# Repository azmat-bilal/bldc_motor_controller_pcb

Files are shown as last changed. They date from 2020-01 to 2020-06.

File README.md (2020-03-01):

# bldc_motor_controller_pcb
A Brushless DC Motor controller board. The design is inspired and is compatible with Odrive project (https://github.com/madcowswe/ODriveHardware) except that this one is single channel.

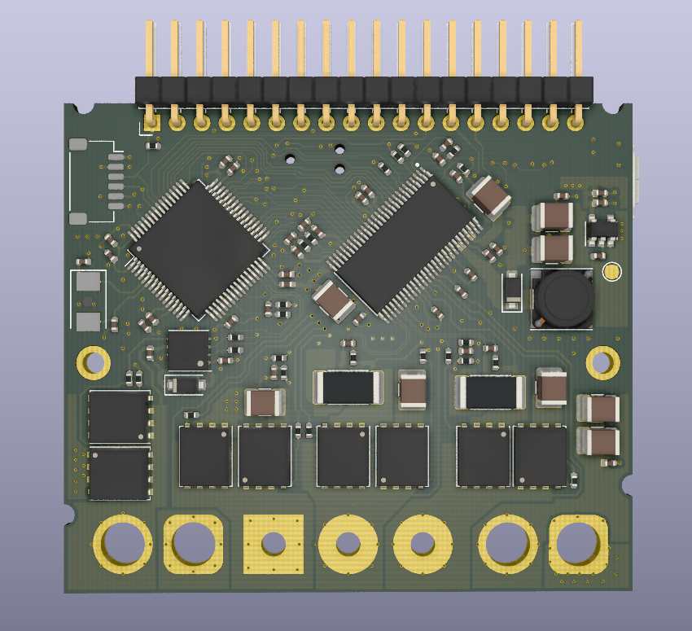
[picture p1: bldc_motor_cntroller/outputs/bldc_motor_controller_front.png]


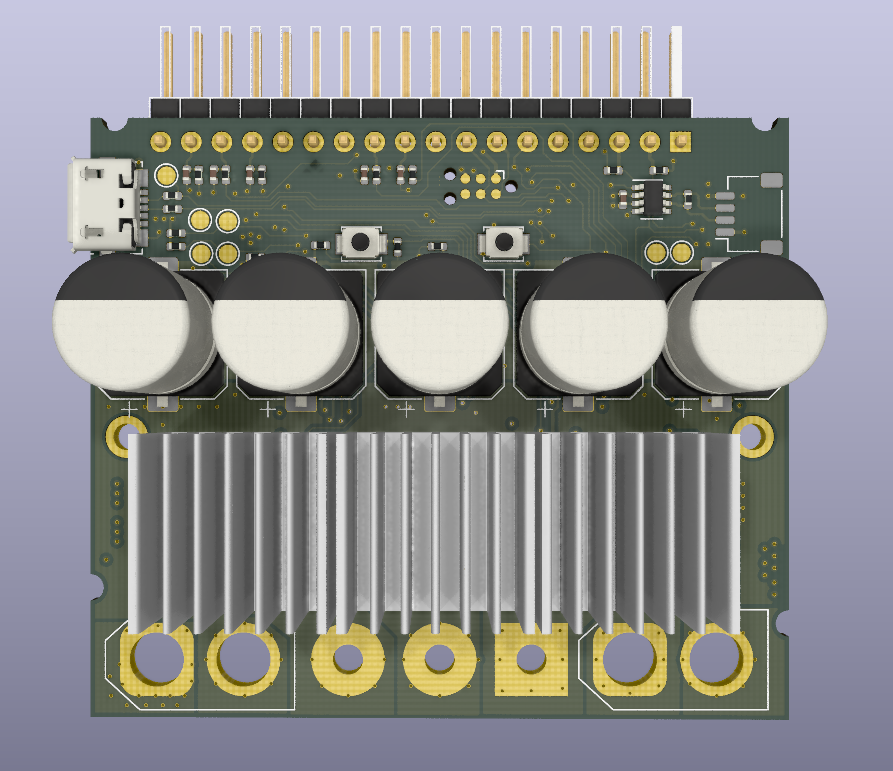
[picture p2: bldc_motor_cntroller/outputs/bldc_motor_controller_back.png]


# Sponsorship
Huge thanks to Mouser Elecotronics (www.mouser.com) to sponsor components to build and test the design.

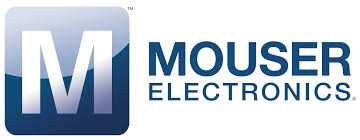
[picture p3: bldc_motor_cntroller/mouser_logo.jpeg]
Sponsor


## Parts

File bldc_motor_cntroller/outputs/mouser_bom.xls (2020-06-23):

BASKET:02.03.2020 00:00:16
Mouser No | Mfr. No | Manufacturer | Customer No | Description | RoHS | Lifecycle | Order Qty. | Price (EUR) | Ext.: (EUR)
80-C0402C223K5R7411 | C0402C223K5RAC7411 | KEMET |  | Multilayer Ceramic Capacitors MLCC - SMD/SMT 50V 0.022uF X7R 0402 10% | RoHS Compliant |  | 2 | 0,234 € | 0,47 €
80-C0402C222J3GECLR | C0402C222J3GEC7411 | KEMET | C37, C41, C45, C46 | Multilayer Ceramic Capacitors MLCC - SMD/SMT 25V 2200pF C0G 0402 5% AEC-Q200 | RoHS Compliant |  | 8 | 0,171 € | 1,37 €
80-C1210C225K1RAUTO | C1210C225K1RACAUTO | KEMET | C42, C43, C44 | Multilayer Ceramic Capacitors MLCC - SMD/SMT 100V 2.2uF X7R 1210 10% AEC-Q200 | RoHS Compliant |  | 6 | 0,603 € | 3,62 €
667-EEH-ZS1J151P | EEH-ZS1J151P | Panasonic | C7, C8, C9, C10, C58 | Aluminium Organic Polymer Capacitors 63VDC 150uF 125degC Hybrid Cap AEC-Q200 | RoHS Compliant | New Product | 10 | 1,47 € | 14,70 €
81-GCM155L8EH104KE7D | GCM155L8EH104KE07D | Murata | C28, C29, C31, C32 | Multilayer Ceramic Capacitors MLCC - SMD/SMT | RoHS Compliant |  | 8 | 0,09 € | 0,72 €
81-GCM155R71E153JA5D | GCM155R71E153JA55D | Murata | C40 | Multilayer Ceramic Capacitors MLCC - SMD/SMT 0402 0.015uF 25volts X7R 5% | RoHS Compliant |  | 2 | 0,09 € | 0,18 €
81-GCQ1555C1H120FB1D | GCQ1555C1H120FB01D | Murata | C56, C57 | Multilayer Ceramic Capacitors MLCC - SMD/SMT 0402 50VDC 12pF 1% AEC-Q200 | RoHS Compliant |  | 4 | 0,486 € | 1,94 €
963-GMK105CC6105MV-F | GMK105CC6105MV-F | Taiyo Yuden | C2 | Multilayer Ceramic Capacitors MLCC - SMD/SMT 0402 35VDC 1uF 20% X6S | RoHS Compliant | New Product | 14 | 0,094 € | 1,32 €
81-GRM1555C1H271FA1D | GRM1555C1H271FA01D | Murata | C14, C39 | Multilayer Ceramic Capacitors MLCC - SMD/SMT 270pF 50Volts C0G 1% | RoHS Compliant |  | 4 | 0,189 € | 0,76 €
81-GRM155C81E225KE1D | GRM155C81E225KE11D | Murata | C15, C21 | Multilayer Ceramic Capacitors MLCC - SMD/SMT 0402 2.2uF 25volts *Derate Voltage/Temp | RoHS Compliant |  | 12 | 0,165 € | 1,98 €
81-GRM155R62A104KE4D | GRM155R62A104KE14D | Murata | C1 | Multilayer Ceramic Capacitors MLCC - SMD/SMT 0402 0.10uF 100volts *Derate Voltage/Temp | RoHS Compliant |  | 26 | 0,032 € | 0,83 €
81-GRM32EC81C476KE5L | GRM32EC81C476KE15L | Murata | C34, C35 | Multilayer Ceramic Capacitors MLCC - SMD/SMT 1210 47uF 16volts *Derate Voltage/Temp | RoHS Compliant |  | 4 | 0,702 € | 2,81 €
963-HMK325C7475KN-TE | HMK325C7475KN-TE | Taiyo Yuden | C25, C27 | Multilayer Ceramic Capacitors MLCC - SMD/SMT 1210 100VDC 4.7uF 10% X7S | RoHS Compliant |  | 4 | 1,13 € | 4,52 €
77-VJ0402A820JXACBC | VJ0402A820JXACW1BC | Vishay | C1, C2, C3, C4, C5, C | Multilayer Ceramic Capacitors MLCC - SMD/SMT 0402 82pF 50volts C0G 5% | RoHS Compliant |  | 12 | 0,09 € | 1,08 €
71-CRCW04020000Z0EDC | CRCW04020000Z0EDC | Vishay | R1, R2, R6, R7, R8 | Thick Film Resistors - SMD 1/16watt 0ohm Commercial Use | RoHS Compliant By Exemption |  | 10 | 0,014 € | 0,14 €
71-CRCW040210K0FKEDC | CRCW040210K0FKEDC | Vishay | R11, R13, R25, R26, R | Thick Film Resistors - SMD 1/16watt 10Kohms 1% Commercial Use | RoHS Compliant By Exemption |  | 14 | 0,029 € | 0,41 €
71-CRCW0402-18K-E3 | CRCW040218K0FKED | Vishay | R22, R24 | Thick Film Resistors - SMD 1/16watt 18Kohms 1% | RoHS Compliant By Exemption |  | 4 | 0,09 € | 0,36 €
71-CRCW0402220KFKEDC | CRCW0402220KFKEDC | Vishay | R20 | Thick Film Resistors - SMD 1/16watt 220Kohms 1% Commercial Use | RoHS Compliant By Exemption |  | 2 | 0,09 € | 0,18 €
71-CRCW040222R0FKEDC | CRCW040222R0FKEDC | Vishay | R9, R10 | Thick Film Resistors - SMD 1/16watt 22ohms 1% Commercial Use | RoHS Compliant By Exemption |  | 8 | 0,09 € | 0,72 €
71-CRCW04022R20FKEDC | CRCW04022R20FKEDC | Vishay | R15, R18, R33, R34, R | Thick Film Resistors - SMD 1/16watt 2.2ohms 1% Commercial Use | RoHS Compliant By Exemption |  | 16 | 0,086 € | 1,38 €
71-CRCW04023K30FKEDC | CRCW04023K30FKEDC | Vishay | R3, R4, R5, R16, R17, | Thick Film Resistors - SMD 1/16watt 3.3Kohms 1% Commercial Use | RoHS Compliant By Exemption |  | 18 | 0,029 € | 0,52 €
279-CRGP0402F47K | CRGP0402F47K | TE Connectivity | R30 | Thick Film Resistors - SMD CRGP 0402 47K 1% SMD Resistor | RoHS Compliant |  | 2 | 0,09 € | 0,18 €
652-CSS2H2512RL500F | CSS2H-2512R-L500F | Bourns | R41, R42 | Current Sense Resistors - SMD 0.5mOHMS 6W 1% AEC-Q200 | RoHS Compliant |  | 4 | 0,837 € | 3,35 €
667-ERJ-2RKF1001X | ERJ-2RKF1001X | Panasonic | R14, R21 | Thick Film Resistors - SMD 0402 1Kohms 1% AEC-Q200 | RoHS Compliant By Exemption |  | 4 | 0,09 € | 0,36 €
667-ERJ-2RKF1200X | ERJ-2RKF1200X | Panasonic | R12, R39, R40 | Thick Film Resistors - SMD 0402 120ohms 1% AEC-Q200 | RoHS Compliant By Exemption |  | 6 | 0,09 € | 0,54 €
963-NR6045T330M | NR6045T330M | Taiyo Yuden | L1 | Fixed Inductors 6045 33uH 188.5mOhms +/-20%Tol 1.4A HiCur | RoHS Compliant |  | 2 | 0,387 € | 0,77 €
863-MBR140SFT1G | MBR140SFT1G | ON Semiconductor | D1 | Schottky Diodes & Rectifiers 1A 40V | RoHS Compliant |  | 2 | 0,36 € | 0,72 €
863-MBR2H100SFT3G | MBR2H100SFT3G | ON Semiconductor | D2 | Schottky Diodes & Rectifiers 2A 100V | RoHS Compliant |  | 2 | 0,396 € | 0,79 €
595-DRV8301DCAR | DRV8301DCAR | Texas Instruments | U4 | Motor/Motion/Ignition Controllers & Drivers 3-PHASE BRUSHLESS MOTOR PRE-DRIVER | RoHS Compliant |  | 2 | 5,26 € | 10,52 €
926-LM5109BSDX/NOPB | LM5109BSDX/NOPB | Texas Instruments | U3 | Gate Drivers | RoHS Compliant |  | 2 | 1,18 € | 2,36 €
511-STM32F405RGT7 | STM32F405RGT7 | STMicroelectronics | U5 | ARM Microcontrollers - MCU 16/32-BITS MICROS | RoHS Compliant |  | 2 | 9,86 € | 19,72 €
595-TCAN332GDCNT | TCAN332GDCNT | Texas Instruments | U1 | CAN Interface IC | RoHS Compliant |  | 2 | 2,44 € | 4,88 €
595-TLV75733PDBVR | TLV75733PDBVR | Texas Instruments | U2 | LDO Voltage Regulators 1-A low-IQ small-size low-dropout (LDO) regulator 5-SOT-23 -40 to 125 | RoHS Compliant |  | 2 | 0,522 € | 1,04 €
581-CX532GB8HHPQZ1 | CX5032GB08000H0HPQZ1 | Kyocera | Y1 | Crystals 08000kHz 12pF With Thermistor | RoHS Compliant |  | 2 | 0,72 € | 1,44 €
653-B3U-1000P-B | B3U-1000P-B | Omron | SW1, SW2 | Tactile Switches Top Actuated with boss w/o ground | RoHS Compliant |  | 4 | 0,873 € | 3,49 €
595-CSD18540Q5BT | CSD18540Q5BT | Texas Instruments | Q1, Q2, Q3, Q4, Q5, Q | MOSFET 60V,NCh NexFET Pwr MOSFET | RoHS Compliant By Exemption |  | 16 | 2,05 € | 32,80 €
538-47346-0001 | 47346-0001 | Molex | J5 | USB Connectors MICRO USB B RECPT BTTM MOUNT ASSY | RoHS Compliant |  | 2 | 0,855 € | 1,71 €
810-C3225X7R1N106K25 | C3225X7R1N106K250AC | TDK |  | Multilayer Ceramic Capacitors MLCC - SMD/SMT 1210 75VDC 10uF 10% X7R | RoHS Compliant | New Product | 4 | 0,954 € | 3,82 €
985-AS5047P-ATSM | AS5047P-ATSM | ams | U1 | Board Mount Hall Effect/Magnetic Sensors 14 bit core res Up to 28krpm | RoHS Compliant |  | 2 | 10,72 € | 21,44 €

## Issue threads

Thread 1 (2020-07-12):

Rough cost estimate of 10 boards

happytm, 2020-07-12:
can you please provide rough estimate of 10 boards including parts  & PCB's ?

Thanks.

azmat-bilal, 2020-08-24:
i have added mouser BOM (with mouser part numbers). it can be used to estimate realtime cost for 10 units using https://eu.mouser.com/create-bom/

azmat-bilal, 2020-08-24:
for PCBs, it depends on the manufacturer and leadtime. its a simple 4 layer pcb so shouldnt cost more than 200 euros.

happytm, 2020-08-24:
@azmat-bilal  Thanks.

Closed 2020-08-24.

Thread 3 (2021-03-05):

Corresponding to which version and voltage of ODrive?

TDA-2030, 2021-03-05:
Recently, I plan to flash firmware to the board, but I can't find version info on silk screen, so I don't know which firmware to download [here](https://github.com/odriverobotics/ODrive/releases). Please point out the correct firmware.

azmat-bilal, 2021-03-17:
i have tested it with v0.4.1. it should also work with v0.4.11.

for versions v0.5+ it will not work out of the box as there is a firmware change were the controller waits for both drivers to get online at boot. there is a short fix mentioned in detail here https://discourse.odriverobotics.com/t/solved-new-firmware-odrive-tool-v5-1-for-3-4-24v-custom-board-one-axis/5805

Closed 2021-03-17.

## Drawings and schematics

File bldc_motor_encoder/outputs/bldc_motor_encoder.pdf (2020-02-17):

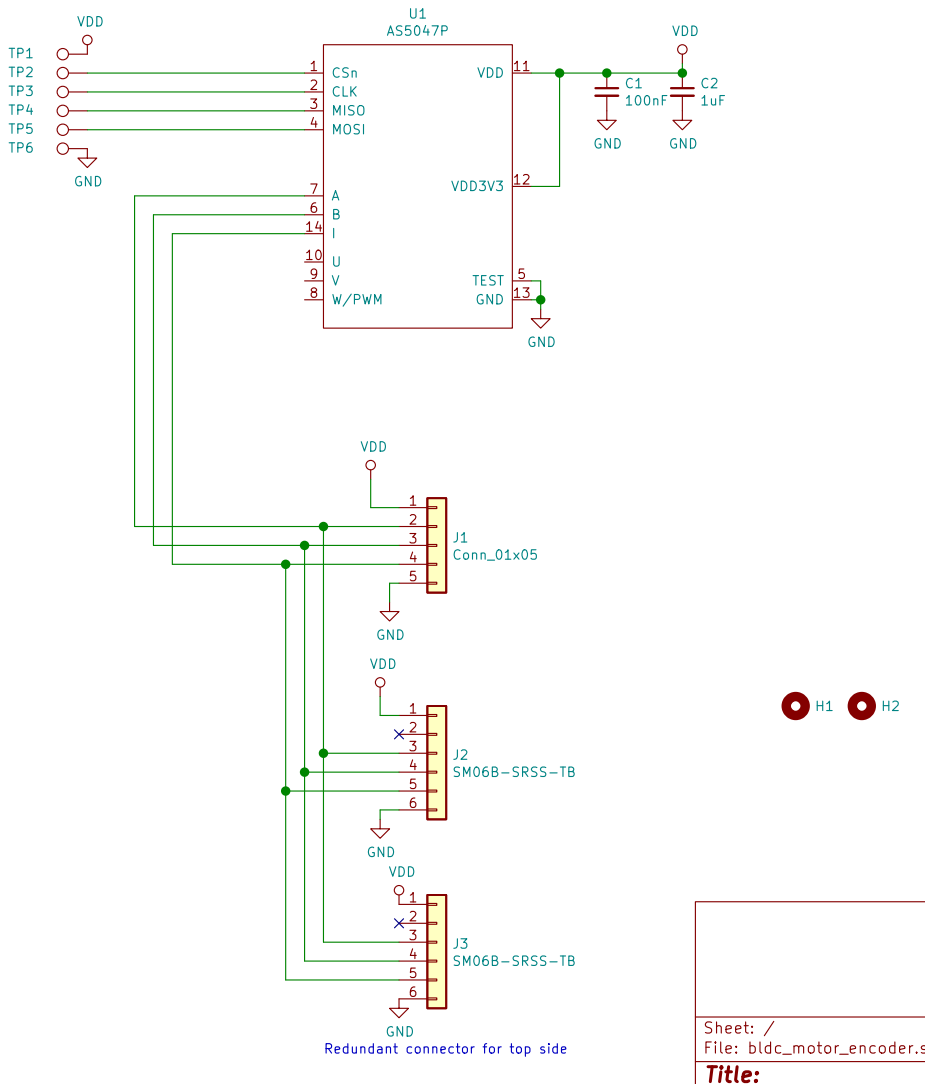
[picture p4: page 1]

1uF Redundant connector for top side

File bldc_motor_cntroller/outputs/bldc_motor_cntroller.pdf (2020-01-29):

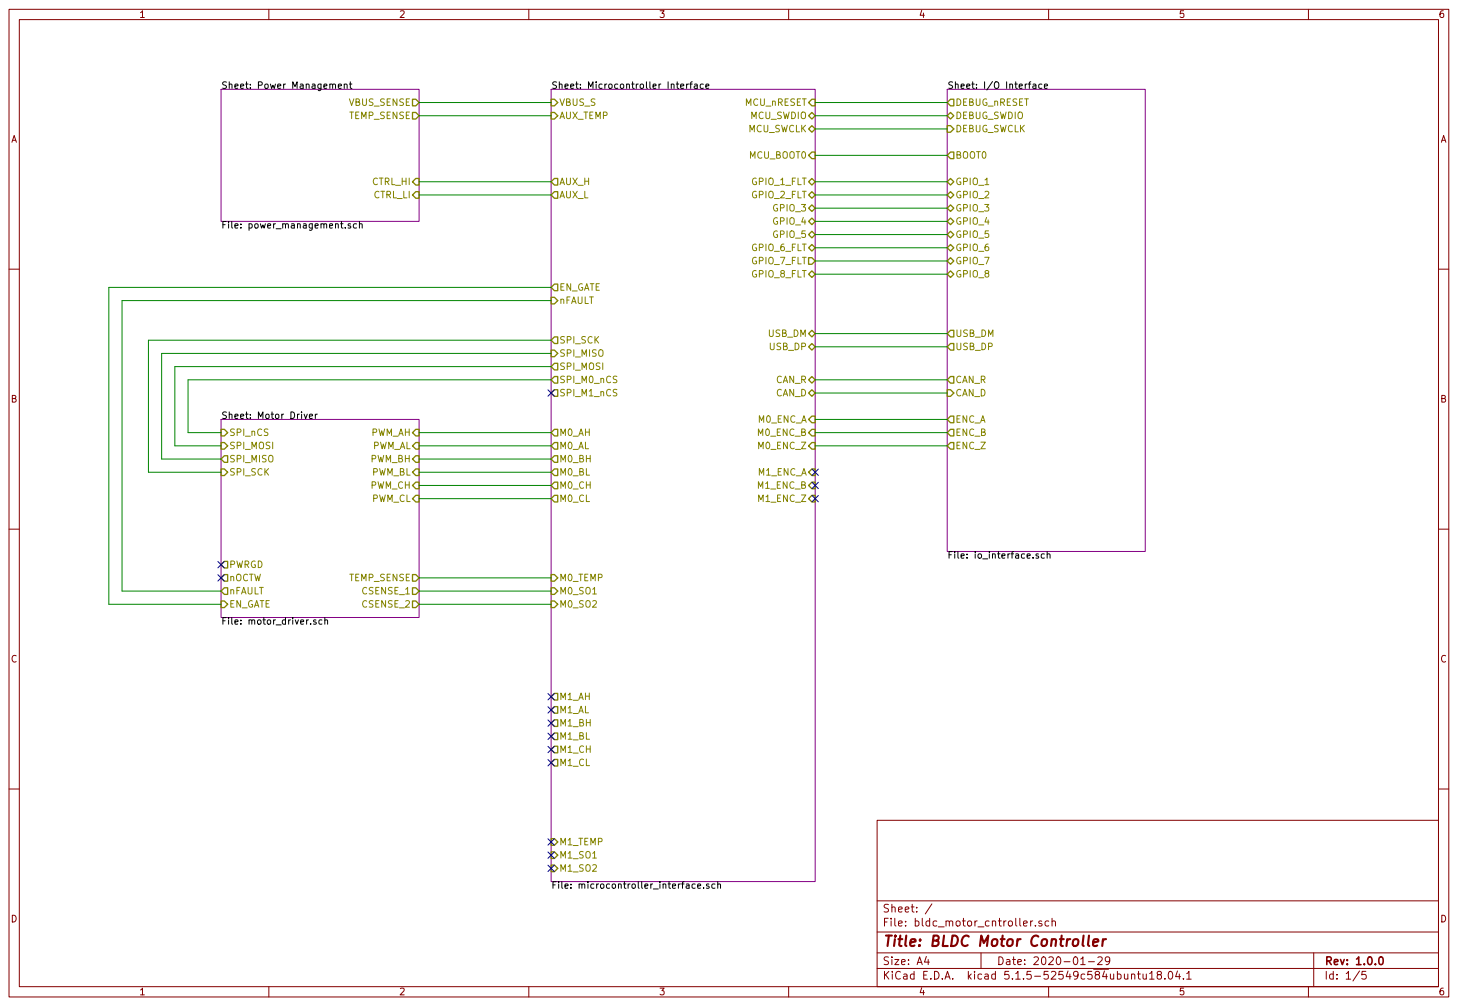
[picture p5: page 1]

Sheet: I/O Interface File: io_interface.sch GPIO_1 GPIO_2 GPIO_7 GPIO_8 GPIO_3 GPIO_6 GPIO_4 GPIO_5 DEBUG_SWDIO
DEBUG_SWCLK DEBUG_nRESET BOOT0 USB_DP USB_DM

File: bldc_motor_cntroller.sch Sheet: /
Id: 1/5 Title: BLDC Motor Controller

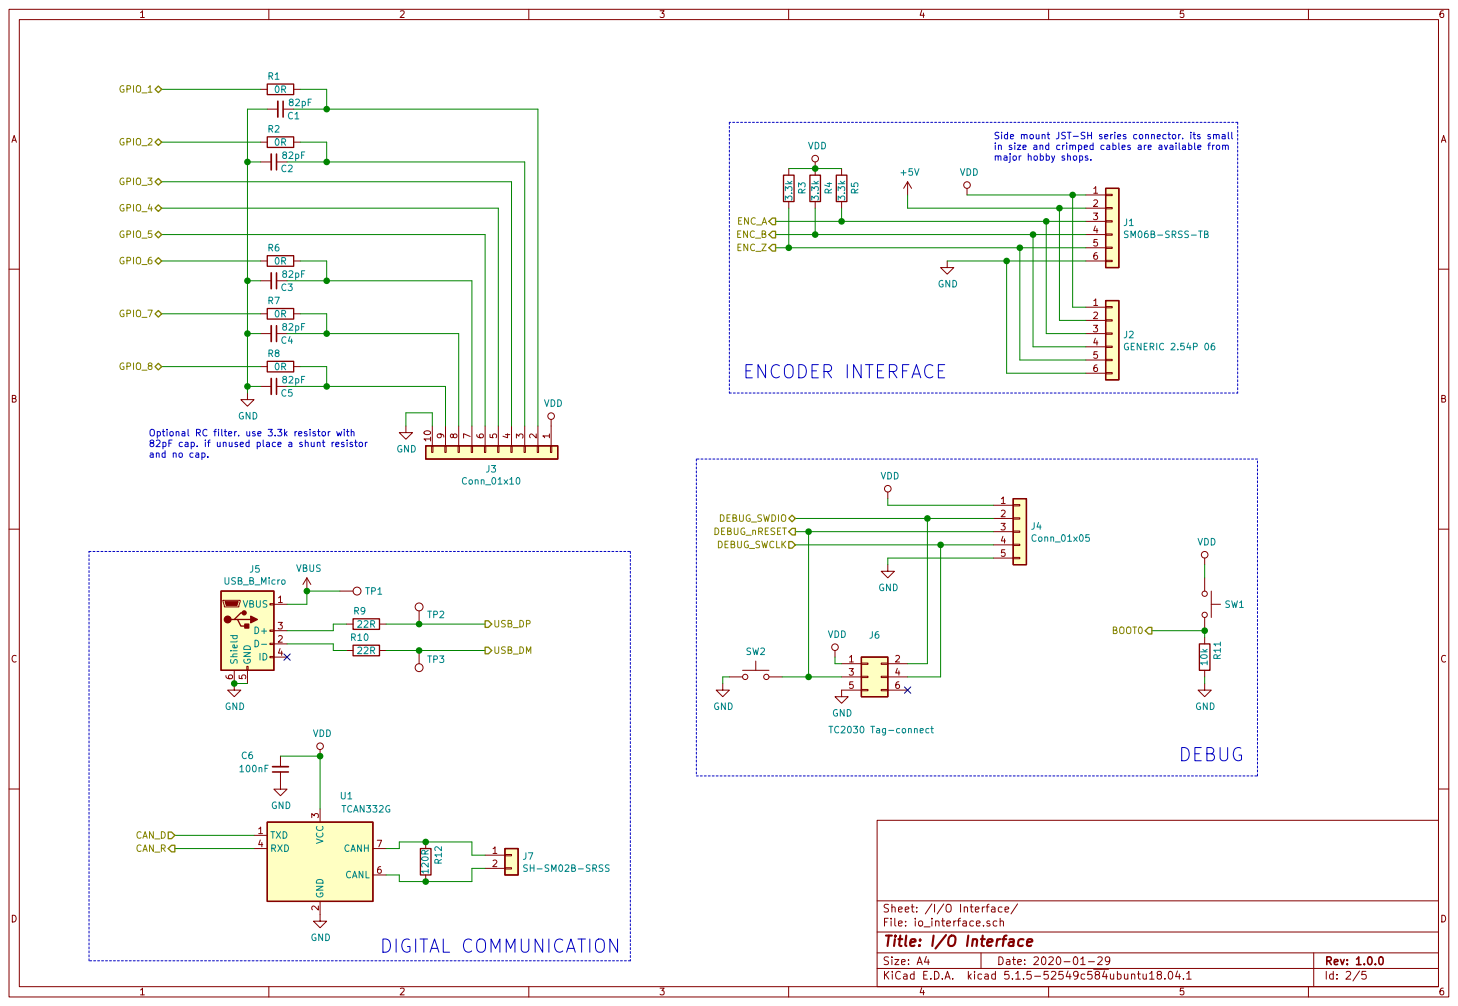
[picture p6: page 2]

Side mount JST-SH series connector. its small
in size and crimped cables are available from
major hobby shops.

Optional RC filter. use 3.3k resistor with
82pF cap. if unused place a shunt resistor
and no cap.

File: io_interface.sch Sheet: /I/O Interface/ GND

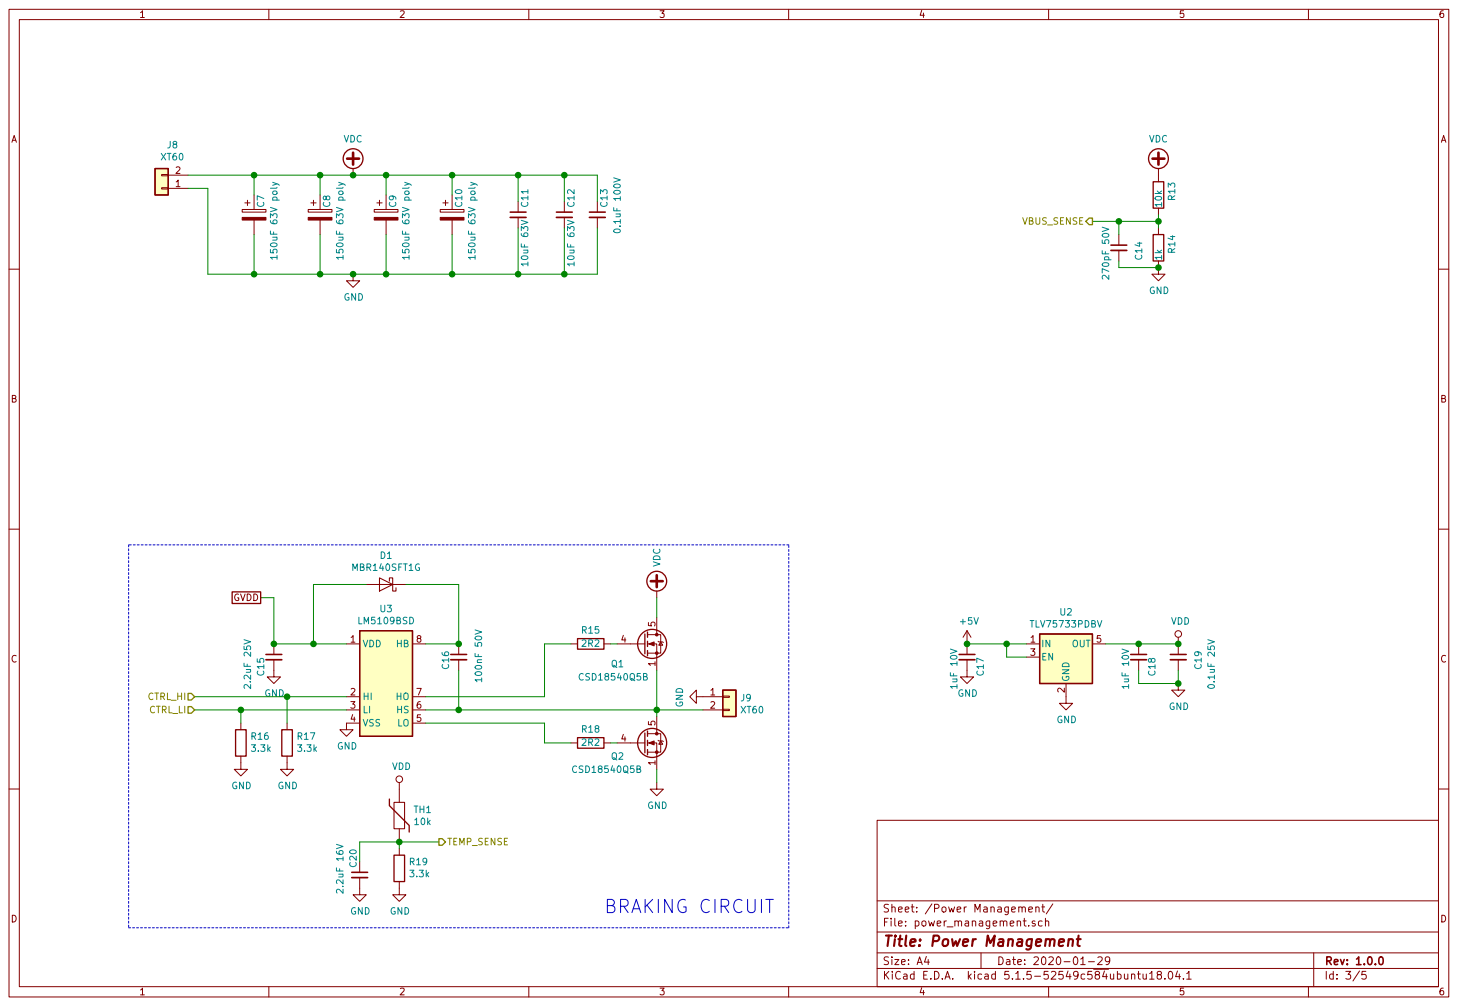
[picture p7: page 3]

Sheet: /Power Management/
File: power_management.sch
Id: 3/5 Title: Power Management

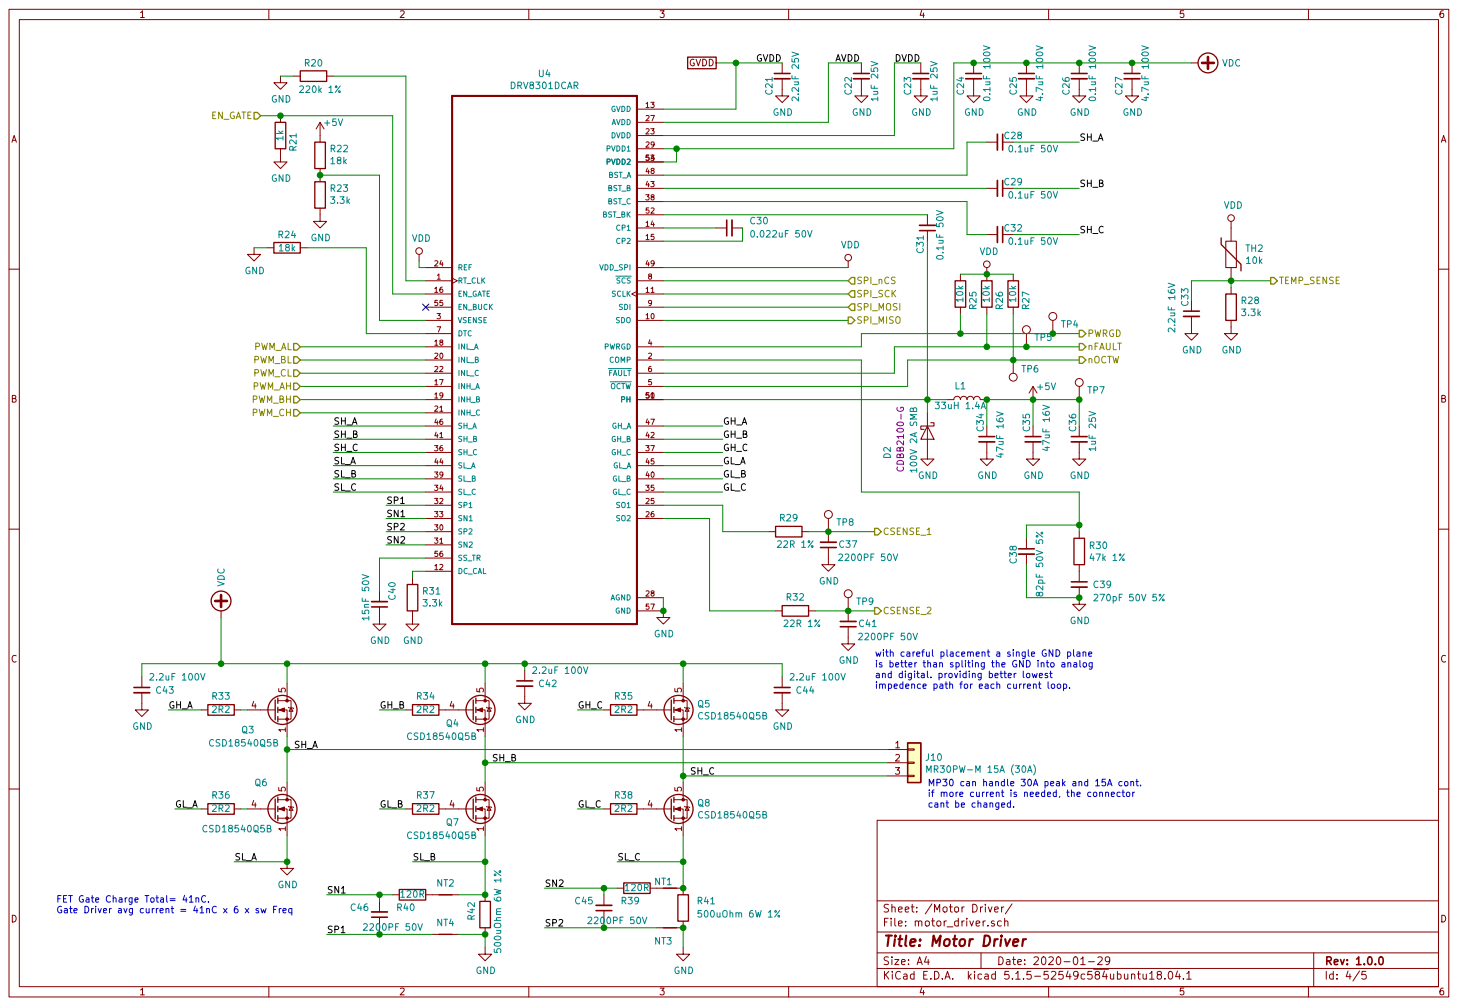
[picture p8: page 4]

with careful placement a single GND plane
is better than spliting the GND into analog
and digital. providing better lowest
impedence path for each current loop.

if more current is needed, the connector cant be changed.

File: motor_driver.sch Sheet: /Motor Driver/ 1

FET Gate Charge Total= 41nC.
Gate Driver avg current = 41nC x 6 x sw Freq

Id: 4/5 Title: Motor Driver

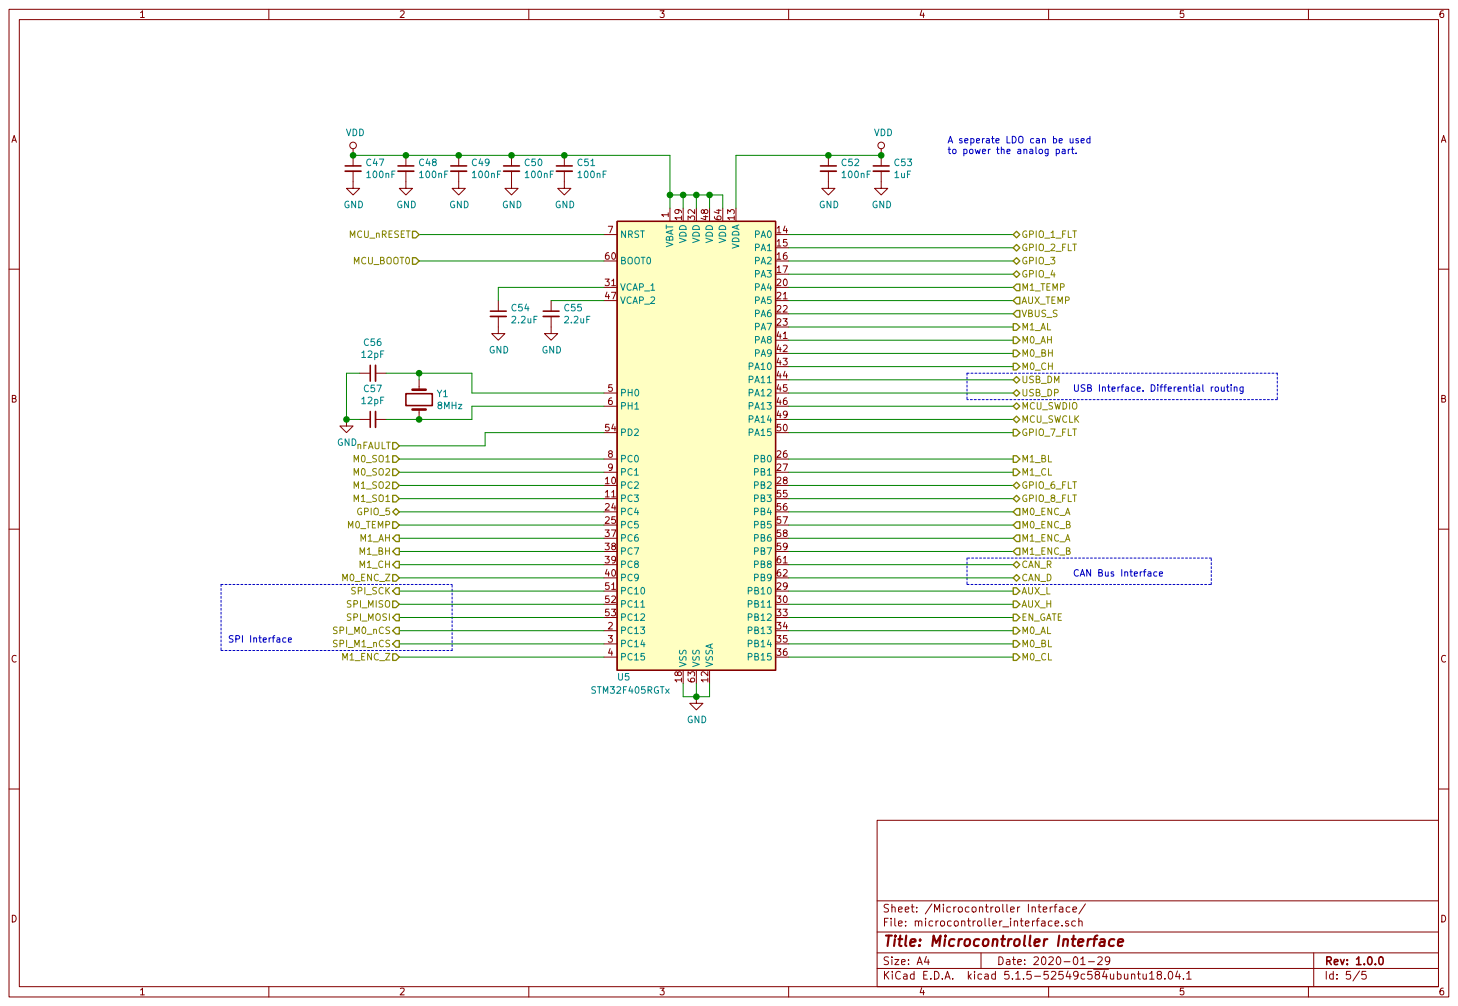
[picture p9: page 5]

A seperate LDO can be used
to power the analog part.

1 VCAP_1 31 VCAP_2 47 VDD 19 VDD 32 VDD 48 VDD 64 VDDA 13 VSS 18 VSS 63 VSSA U5 12 STM32F405RGTx

USB Interface. Differential routing

File: microcontroller_interface.sch Sheet: /Microcontroller Interface/
Id: 5/5 Title: Microcontroller Interface

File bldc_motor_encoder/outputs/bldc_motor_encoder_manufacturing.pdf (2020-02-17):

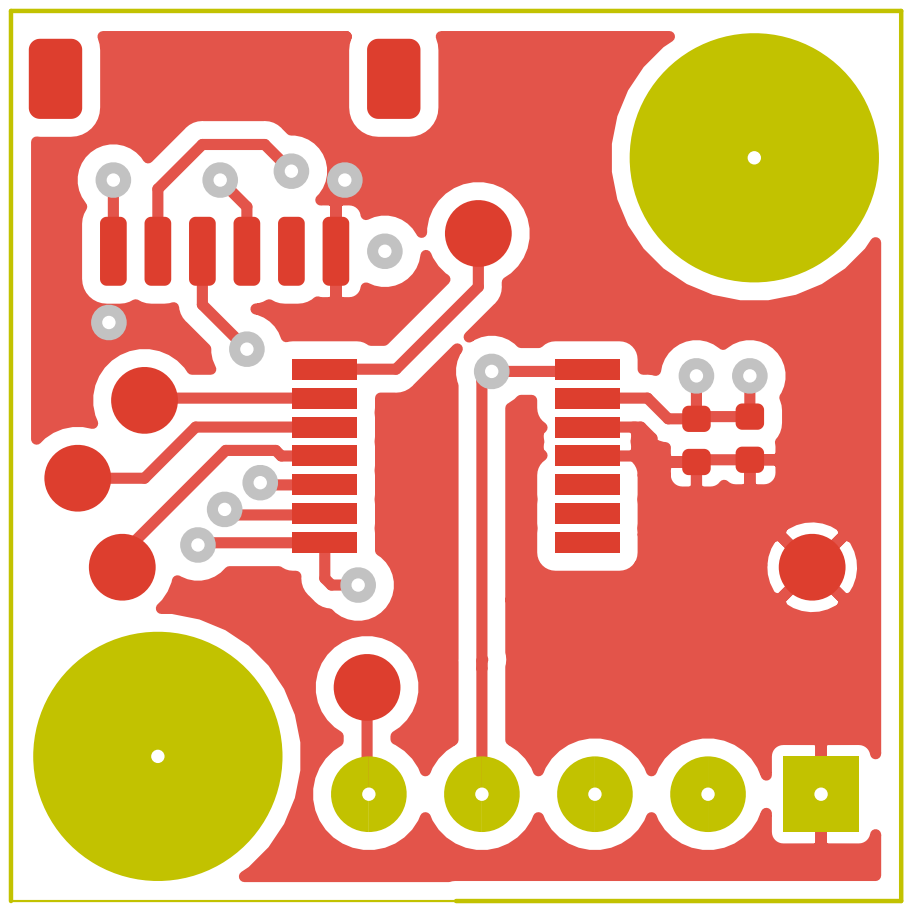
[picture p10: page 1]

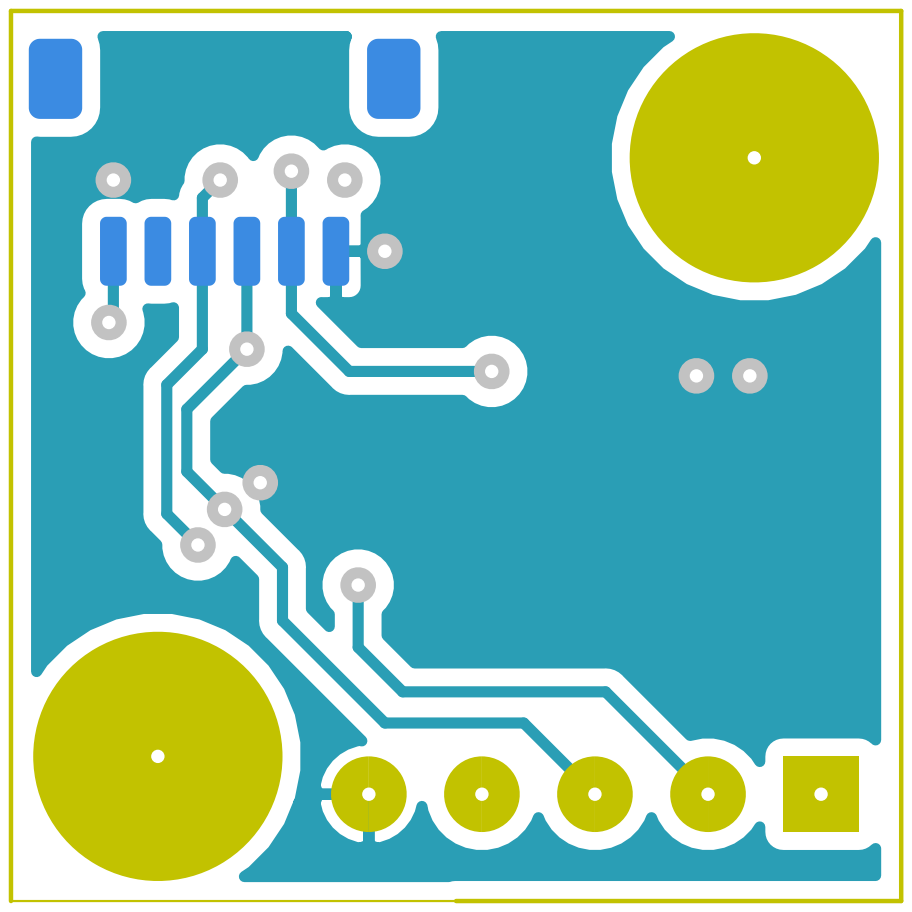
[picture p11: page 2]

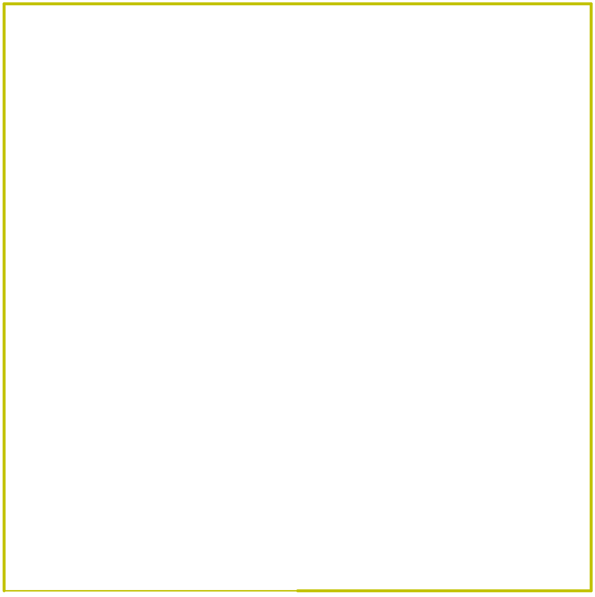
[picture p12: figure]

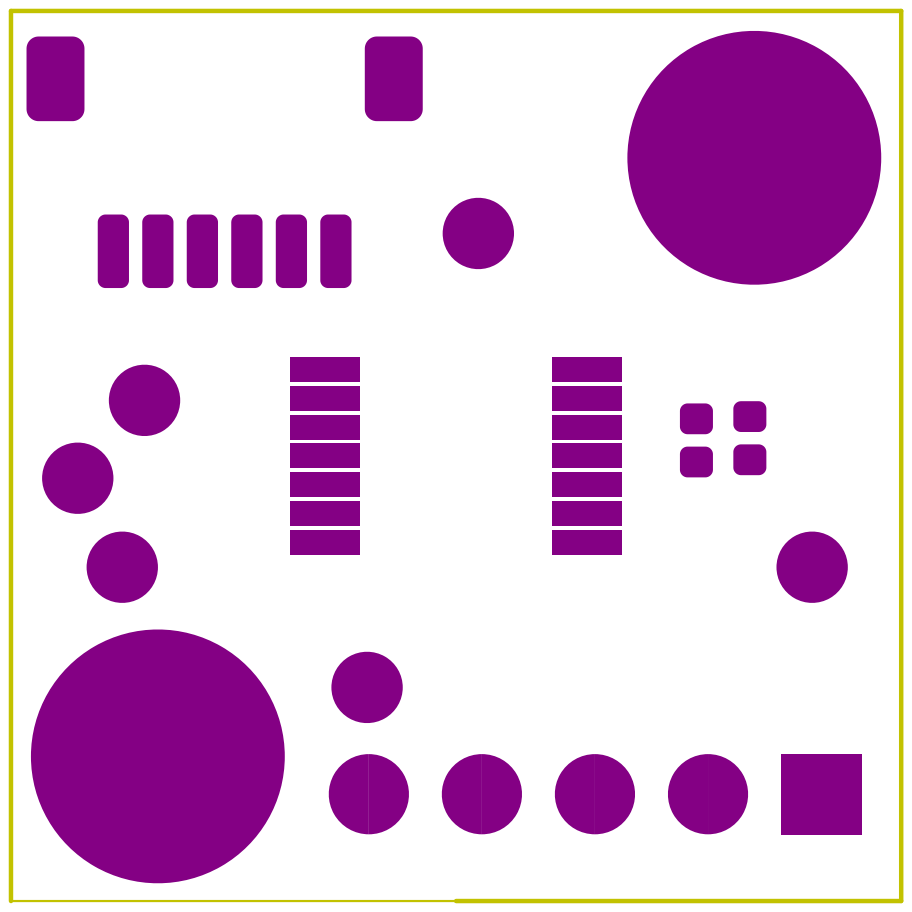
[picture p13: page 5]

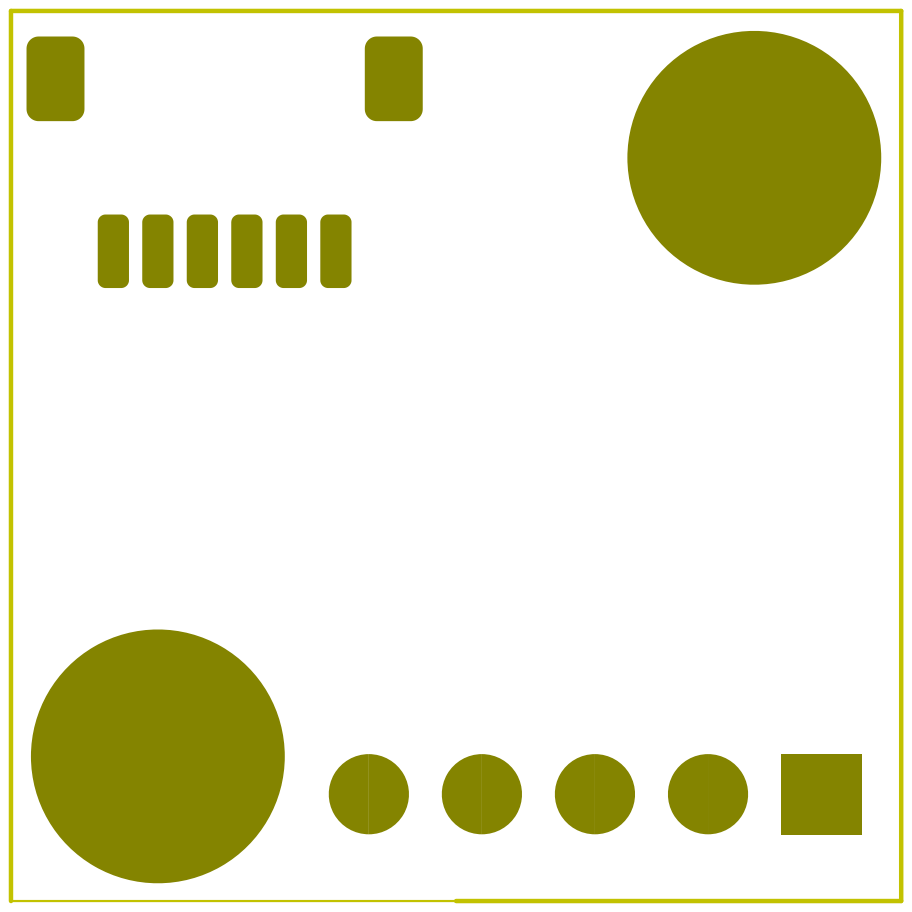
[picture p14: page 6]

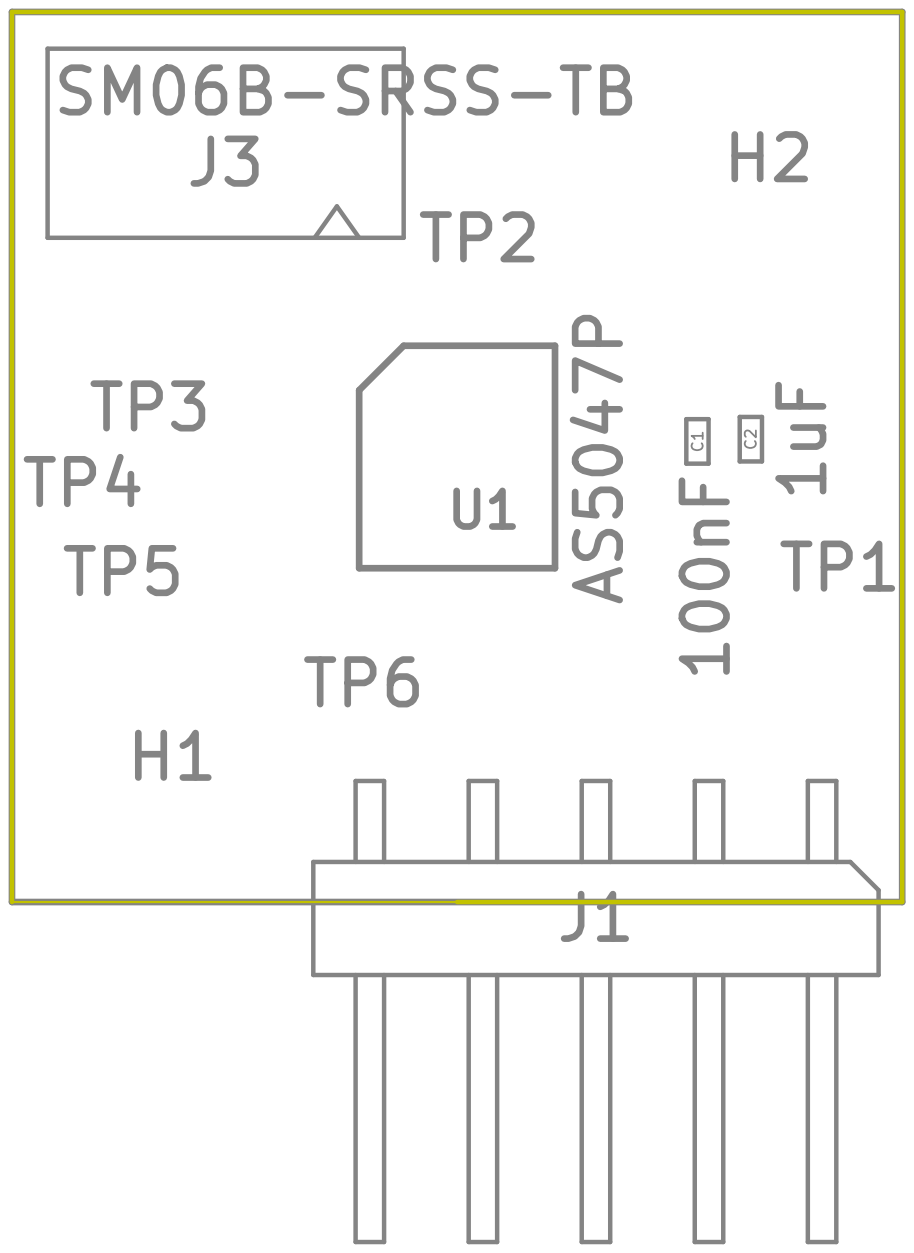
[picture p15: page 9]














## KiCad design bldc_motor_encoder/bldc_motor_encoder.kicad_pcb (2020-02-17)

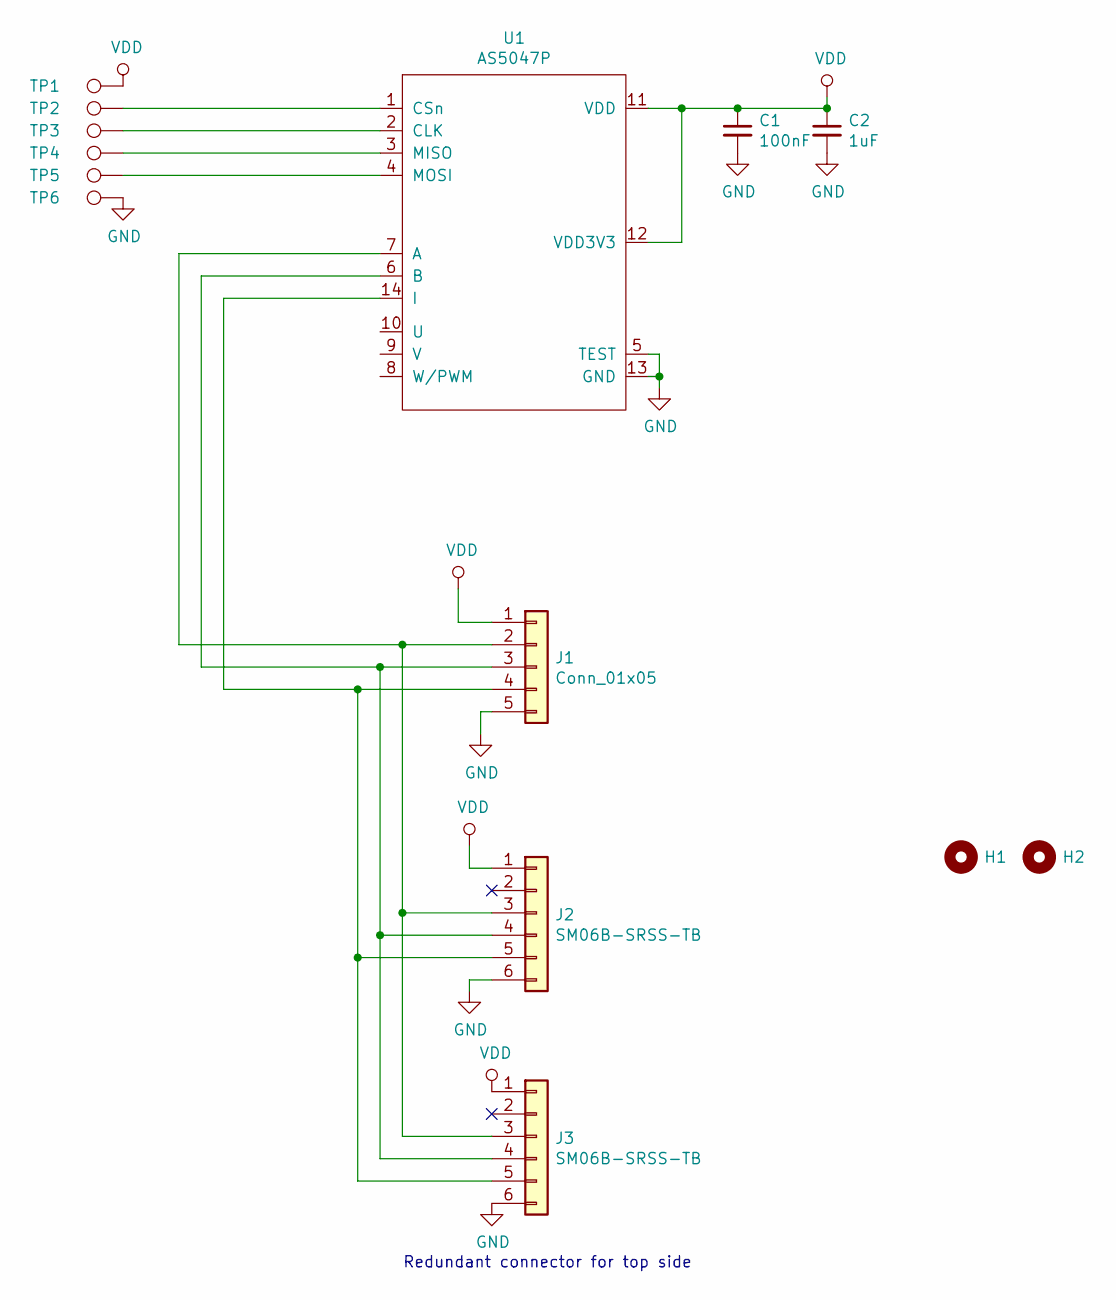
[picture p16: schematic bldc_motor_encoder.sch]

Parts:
C1: 100nF; C_0402_1005Metric
C2: 1uF; C_0402_1005Metric
H1, H2: MountingHole; MountingHole_3.2mm_M3_DIN965_Pad
J1: Conn_01x05; PinHeader_1x05_P2.54mm_Horizontal
J2, J3: SM06B-SRSS-TB; JST_SH_SM06B-SRSS-TB_1x06-1MP_P1.00mm_Horizontal
TP1, TP2, TP3, TP4, TP5, TP6: TestPoint; TestPoint_Pad_D1.5mm
U1: AS5047P; TSSOP-14_4.4x5mm_P0.65mm

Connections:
GND: C1.2, C2.2, J1.5, J2.6, J3.6, TP6.1, U1.5 (TEST), U1.13 (GND)
unnamed: J1.2, J2.3, J3.3, U1.7 (A)
unnamed: J1.3, J2.4, J3.4, U1.6 (B)
unnamed: J1.4, J2.5, J3.5, U1.14 (I)
unnamed: TP2.1, U1.1 (CSn)
unnamed: TP3.1, U1.2 (CLK)
unnamed: TP4.1, U1.3 (MISO)
unnamed: TP5.1, U1.4 (MOSI)
VDD: C1.1, C2.1, J1.1, J2.1, J3.1, TP1.1, U1.11 (VDD), U1.12 (VDD3V3)

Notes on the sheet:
Redundant connector for top side

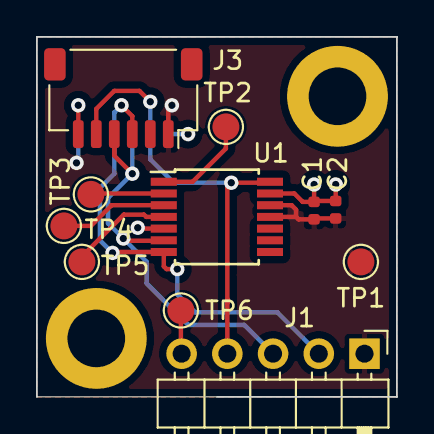
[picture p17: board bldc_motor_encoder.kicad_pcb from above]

Board: 2 copper layers, 20.0 x 20.0 mm, 14 parts (1 on the bottom side), 9 nets.

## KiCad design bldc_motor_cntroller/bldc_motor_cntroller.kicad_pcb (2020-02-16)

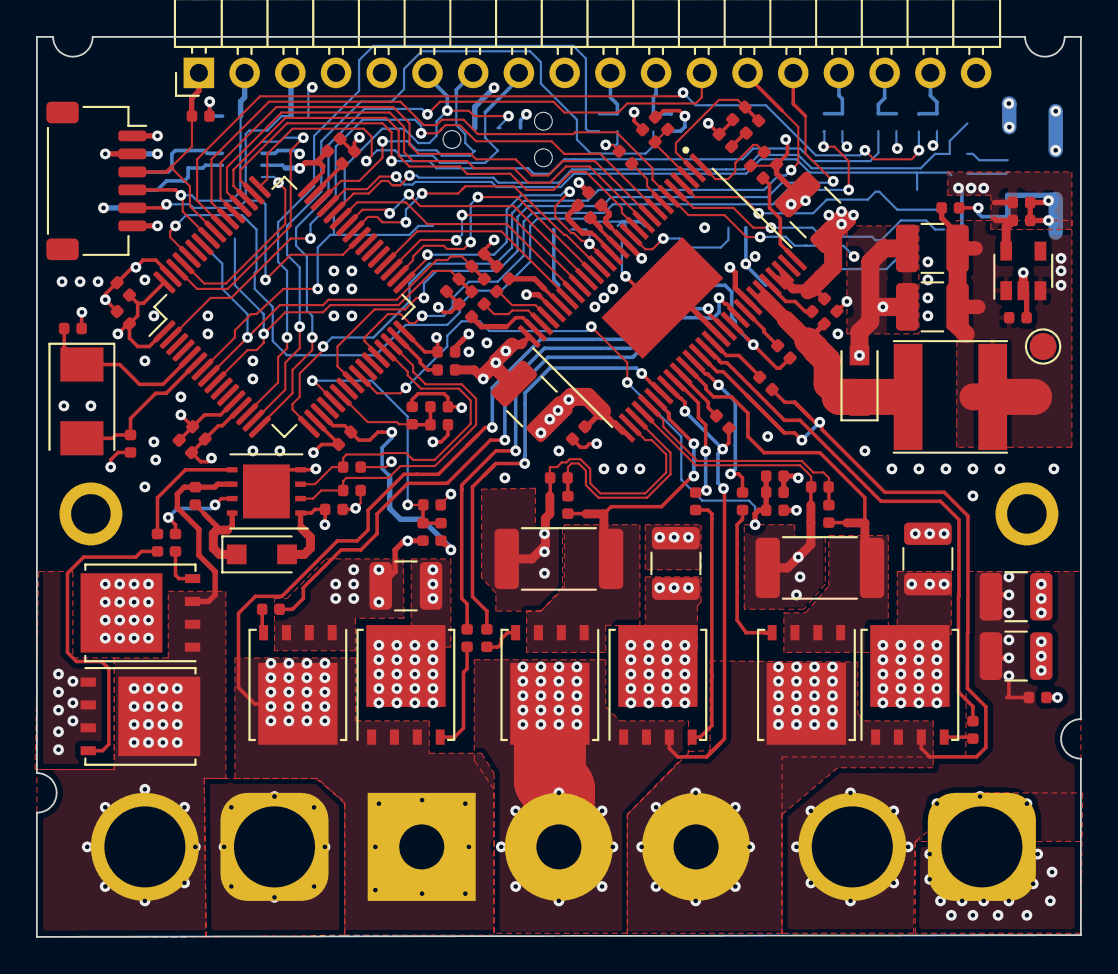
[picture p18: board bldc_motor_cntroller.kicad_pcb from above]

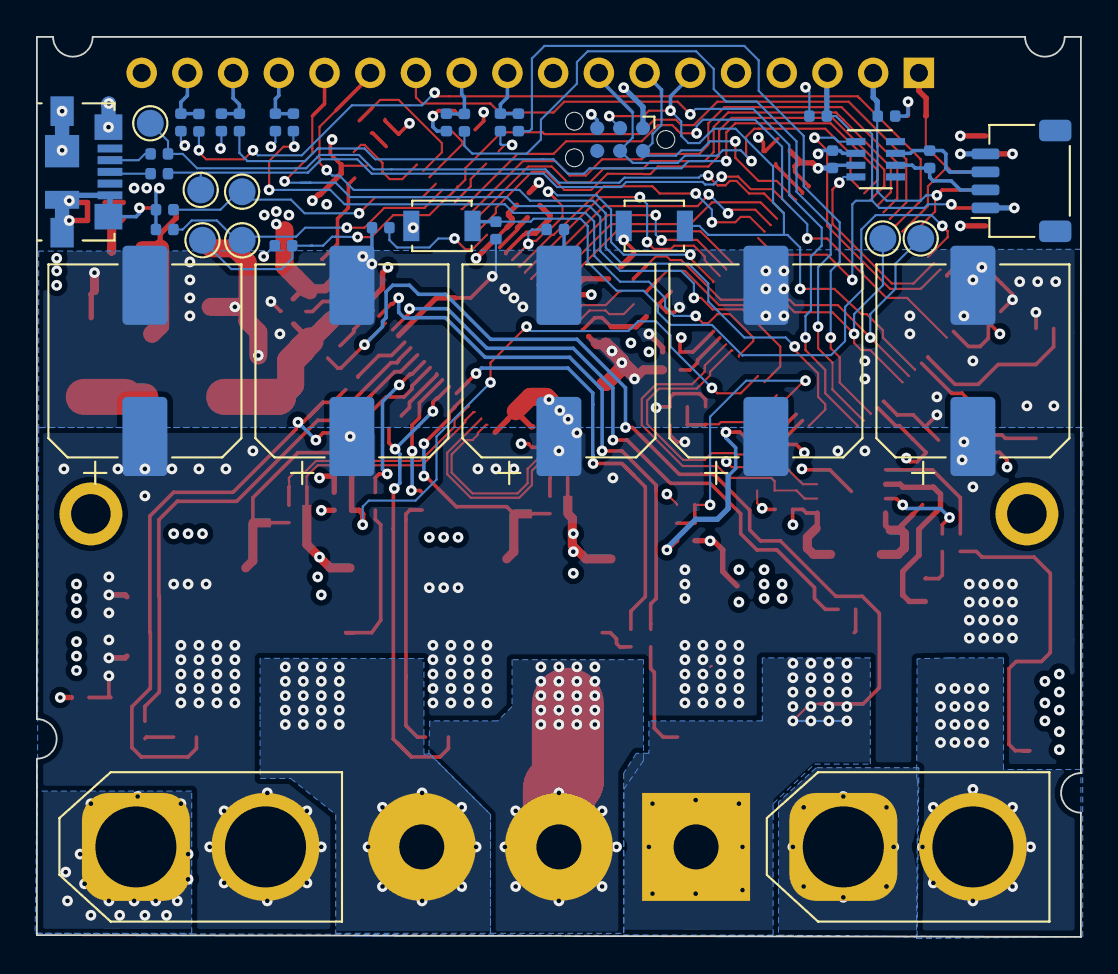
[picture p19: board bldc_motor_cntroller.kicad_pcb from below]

Board: 4 copper layers, 58.0 x 50.0 mm, 146 parts (46 on the bottom side), 105 nets.

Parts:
C1, C2, C3, C4, C5, C38: 82pF; C_0402_1005Metric
C6, C16, C47, C48, C49, C50, C51, C52: 100nF; C_0402_1005Metric
C7, C8, C9, C10, C58: 150uF 63V poly; CP_Elec_10x14.3
C11, C12: 10uF 63V; C_1210_3225Metric
C13, C24, C26: 0.1uF 100V; C_0402_1005Metric
C14, C39: 270pF; C_0402_1005Metric
C15, C21: 2.2uF 25V; C_0402_1005Metric
C17, C18: 1uF 10V; C_0402_1005Metric
C19: 0.1uF 25V; C_0402_1005Metric
C20, C33: 2.2uF 16V; C_0402_1005Metric
C22, C23, C36: 1uF 25V; C_0402_1005Metric
C25, C27: 4.7uF 100V; C_1210_3225Metric
C28, C29, C31, C32: 0.1uF 50V; C_0402_1005Metric
C30: 0.022uF 50V; C_0402_1005Metric
C34, C35: 47uF 16V; C_1210_3225Metric
C37, C41: 2200pF; C_0402_1005Metric
C40: 15nF; C_0402_1005Metric
C42, C43, C44: 2.2uF 100V; C_1210_3225Metric
C45, C46: 2200PF; C_0402_1005Metric
C53: 1uF; C_0402_1005Metric
C54, C55: 2.2uF; C_0402_1005Metric
C56, C57: 12pF; C_0402_1005Metric
D1: MBR140SFT1G; D_SOD-123F
D2: 100V 2A SMB; D_SOD-123F
H1, H2: MountingHole_Pad; MountingHole_2.2mm_M2_ISO7380_Pad
HS1, HS2, HS3: Heatsink; heatsink14x14x6
J1: SM06B-SRSS-TB(LF)(SN); JST_SH_SM06B-SRSS-TB_1x06-1MP_P1.00mm_Horizontal
J2: Conn_01x18; PinHeader_1x18_P2.54mm_Horizontal
J3: SM04B-SRSS-TB(LF)(SN); JST_SH_SM04B-SRSS-TB_1x04-1MP_P1.00mm_Horizontal
J5: 0473460001; USB_Micro-B_Molex_47346-0001
J6: TC2030 Tag-connect; Tag-Connect_TC2030-IDC-NL_2x03_P1.27mm_Vertical
J8, J9: XT60; AMASS_XT60-M_1x02_P7.20mm_Vertical
J10: MR30PW-M 15A (30A); SolderWirePad_1x03_P7.62mm_Drill2.5mm
L1: 33uH 1.4A; L_Taiyo-Yuden_NR-60xx
NT1, NT2, NT3, NT4: Net-Tie_2; NetTie-2_SMD_Pad0.5mm
Q1, Q2, Q3, Q4, Q5, Q6, Q7, Q8: CSD18540Q5B; TDSON-8-1
R1, R2, R6, R7, R8: 0R; R_0402_1005Metric
R3, R4, R5, R16, R17, R19, R23, R28, R31: 3.3k; R_0402_1005Metric
R9, R10: 22R; R_0402_1005Metric
R11, R13, R25, R26, R27: 10k; R_0402_1005Metric
R12, R39, R40: 120R; R_0402_1005Metric
R14, R21: 1k; R_0402_1005Metric
R15, R18, R33, R34, R35, R36, R37, R38: 2R2; R_0402_1005Metric
R20: 220k 1%; R_0402_1005Metric
R22, R24: 18k; R_0402_1005Metric
R29, R32: 22R 1%; R_0402_1005Metric
R30: 47k 1%; R_0402_1005Metric
R41, R42: 500uOhm 6W 1%; R_2512_6332Metric
SW1, SW2: B3U-1000P-B; SW_SPST_B3U-1000P
TH1, TH2: 10k; R_0402_1005Metric
TP2, TP3, TP4, TP5, TP6, TP7, TP8, TP9: TestPoint; TestPoint_Pad_D1.5mm
U1: TCAN332GDCNT; SOT-23-8
U2: TLV75733PDBV; SOT-23-5
U3: LM5109BSD; WSON-8_4x4mm_P0.8mm
U4: DRV8301DCAR; SOP50P810X120-57N
U5: STM32F405RGTx; LQFP-64_10x10mm_P0.5mm
Y1: 8MHz; Crystal_SMD_Abracon_ABM3-2Pin_5.0x3.2mm

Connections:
+5V: C17.1, C34.1, C35.1, C36.1, J1.2, J2.4, L1.2, R22.2, TP7.1, U2.1, U2.3
/I/O Interface/BOOT0: R11.2, SW1.2, U5.60
/I/O Interface/CAN_D: U1.1, U5.62
/I/O Interface/CAN_R: U1.4, U5.61
/I/O Interface/DEBUG_SWCLK: J2.8, J6.4, U5.49
/I/O Interface/DEBUG_SWDIO: J2.7, J6.2, U5.46
/I/O Interface/DEBUG_nRESET: J2.6, J6.3, SW2.2, U5.7
/I/O Interface/ENC_A: J1.3, J2.1, R5.2, U5.56
/I/O Interface/ENC_B: J1.4, J2.2, R4.2, U5.57
/I/O Interface/ENC_Z: J1.5, J2.3, R3.2, U5.40
/I/O Interface/GPIO_1: R1.2, U5.14
/I/O Interface/GPIO_2: R2.2, U5.15
/I/O Interface/GPIO_3: J2.12, U5.16
/I/O Interface/GPIO_4: J2.13, U5.17
/I/O Interface/GPIO_5: J2.14, U5.24
/I/O Interface/GPIO_6: R6.2, U5.28
/I/O Interface/GPIO_7: R7.2, U5.50
/I/O Interface/GPIO_8: R8.2, U5.55
/I/O Interface/USB_DM: R10.1, TP3.1, U5.44
/I/O Interface/USB_DP: R9.1, TP2.1, U5.45
/Microcontroller Interface/AUX_H: R17.2, U3.2, U5.30
/Microcontroller Interface/AUX_L: R16.2, U3.3, U5.29
/Microcontroller Interface/AUX_TEMP: C20.1, R19.2, TH1.2, U5.21
/Microcontroller Interface/EN_GATE: R21.2, U4.16, U5.33
/Microcontroller Interface/M0_AH: U4.17, U5.41
/Microcontroller Interface/M0_AL: U4.18, U5.34
/Microcontroller Interface/M0_BH: U4.19, U5.42
/Microcontroller Interface/M0_BL: U4.20, U5.35
/Microcontroller Interface/M0_CH: U4.21, U5.43
/Microcontroller Interface/M0_CL: U4.22, U5.36
/Microcontroller Interface/M0_TEMP: C33.1, R28.2, TH2.2, U5.25
/Microcontroller Interface/SPI_M0_nCS: U4.8, U5.2
/Microcontroller Interface/SPI_MISO: U4.10, U5.52
/Microcontroller Interface/SPI_MOSI: U4.9, U5.53
/Microcontroller Interface/SPI_SCK: U4.11, U5.51
/Microcontroller Interface/VBUS_S: C14.1, R13.2, R14.1, U5.22
/Microcontroller Interface/nFAULT: R26.1, TP5.1, U4.6, U5.54
/Motor Driver/AVDD: C22.1, U4.27
/Motor Driver/CSENSE_1: C37.2, R29.2, TP8.1, U5.8
/Motor Driver/CSENSE_2: C41.2, R32.2, TP9.1, U5.9
/Motor Driver/DVDD: C23.1, U4.23
/Motor Driver/GH_A: R33.1, U4.47
/Motor Driver/GH_B: R34.1, U4.42
/Motor Driver/GH_C: R35.1, U4.37
/Motor Driver/GL_A: R36.1, U4.45
/Motor Driver/GL_B: R37.1, U4.40
/Motor Driver/GL_C: R38.1, U4.35
/Motor Driver/PWRGD: R25.1, TP4.1, U4.4
/Motor Driver/SH_A: C28.1, J10.1, Q3.1, Q3.2, Q3.3, Q6.5, U4.46
/Motor Driver/SH_B: C29.1, J10.3, Q4.1, Q4.2, Q4.3, Q7.5, U4.41
/Motor Driver/SH_C: C32.1, J10.2, Q5.1, Q5.2, Q5.3, Q8.5, U4.36
/Motor Driver/SL_B: NT2.2, Q7.1, Q7.2, Q7.3, R42.2, U4.39
/Motor Driver/SL_C: NT1.2, Q8.1, Q8.2, Q8.3, R41.2, U4.34
/Motor Driver/SN1: C46.2, R40.1, U4.33
/Motor Driver/SN2: C45.2, R39.1, U4.31
/Motor Driver/SP1: C46.1, NT4.1, U4.32
/Motor Driver/SP2: C45.1, NT3.1, U4.30
/Motor Driver/nOCTW: R27.1, TP6.1, U4.5
GND: C1.2, C2.2, C3.2, C4.2, C5.2, C6.1, C7.2, C8.2, C9.2, C10.2, C11.2, C12.2, C13.2, C14.2, C15.2, C17.2, C18.2, C19.2, C20.2, C21.2, C22.2, C23.2, C24.2, C25.2, C26.2, C27.2, C33.2, C34.2, C35.2, C36.2, C37.1, C38.2, C39.2, C40.1, C41.1, C42.2, C43.2, C44.2, C47.2, C48.2, C49.2, C50.2, C51.2, C52.2, C53.2, C54.2, C55.2, C56.1, C57.1, C58.2, D2.2, J1.6, J2.5, J2.18, J3.4, J5.5, J5.6, J6.5, J8.1, J9.1, NT3.2, NT4.2, Q2.1, Q2.2, Q2.3, Q6.1, Q6.2, Q6.3, R11.1, R14.2, R16.1, R17.1, R19.1, R20.2, R21.1, R23.1, R24.2, R28.1, R31.1, R41.1, R42.1, SW2.1, U1.2, U2.2, U3.4, U3.9, U4.28, U4.44, U4.57, U5.12, U5.18, U5.63
GVDD: C15.1, C21.1, D1.2, U3.1, U4.13
unnamed: C1.1, J2.10, R1.1
unnamed: C2.1, J2.11, R2.1
unnamed: C3.1, J2.15, R6.1
unnamed: C4.1, J2.16, R7.1
unnamed: C5.1, J2.17, R8.1
unnamed: C16.1, D1.1, U3.8
unnamed: C16.2, J9.2, Q1.1, Q1.2, Q1.3, Q2.5, U3.6
unnamed: C28.2, U4.48
unnamed: C29.2, U4.43
unnamed: C30.1, U4.14
unnamed: C30.2, U4.15
unnamed: C31.1, D2.1, L1.1, U4.50, U4.51
unnamed: C31.2, U4.52
unnamed: C32.2, U4.38
unnamed: C38.1, R30.1, U4.2
unnamed: C39.1, R30.2
unnamed: C40.2, U4.56
unnamed: C54.1, U5.31
unnamed: C55.1, U5.47
unnamed: C56.2, U5.5, Y1.1
unnamed: C57.2, U5.6, Y1.2
unnamed: J3.2, R12.1, U1.6
unnamed: J3.3, R12.2, U1.7
unnamed: J5.2, R10.2
unnamed: J5.3, R9.2
unnamed: NT1.1, R39.2
unnamed: NT2.1, R40.2
unnamed: Q1.4, R15.2
unnamed: Q2.4, R18.2
unnamed: Q3.4, R33.2
unnamed: Q4.4, R34.2
unnamed: Q5.4, R35.2
unnamed: Q6.4, R36.2
unnamed: Q7.4, R37.2
unnamed: Q8.4, R38.2
unnamed: R15.1, U3.7
unnamed: R18.1, U3.5
unnamed: R20.1, U4.1
unnamed: R22.1, R23.2, U4.3
unnamed: R24.1, U4.7
unnamed: R29.1, U4.25
unnamed: R31.2, U4.12
unnamed: R32.1, U4.26
VDC: C7.1, C8.1, C9.1, C10.1, C11.1, C12.1, C13.1, C24.1, C25.1, C26.1, C27.1, C42.1, C43.1, C44.1, C58.1, J8.2, Q1.5, Q3.5, Q4.5, Q5.5, R13.1, U4.29, U4.53, U4.54
VDD: C6.2, C18.1, C19.1, C47.1, C48.1, C49.1, C50.1, C51.1, C52.1, C53.1, J1.1, J2.9, J3.1, J6.1, R3.1, R4.1, R5.1, R25.2, R26.2, R27.2, SW1.1, TH1.1, TH2.1, U1.3, U2.5, U4.24, U4.49, U5.1, U5.13, U5.19, U5.32, U5.48, U5.64

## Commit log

2020-01-26 first commit. created the kicad project.
    [bldc_motor_cntroller.kicad_pcb, bldc_motor_cntroller.sch]
2020-01-26 adding sub sheets. completed the mcu interface.
    [io_interface.sch, microcontroller_interface.sch, peripheral_interface.sch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]
2020-01-26 interfacing the drv8301 pre-driver.
    [motor_driver.sch]
2020-01-27 finished motor driver interface.
    [bldc_motor_cntroller.sch, motor_driver.sch]
2020-01-27 added braking circuit. added encoder interface.
    [peripheral_interface.sch]
2020-01-29 schematic annotation. added bulk caps. moved shunt res to powersheet.
    [bldc_motor_cntroller.sch, io_interface.sch, microcontroller_interface.sch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]
2020-01-29 added page titles and rev. no.
    [bldc_motor_cntroller.sch, io_interface.sch, microcontroller_interface.sch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]
2020-01-29 removed redundant files.
    [peripheral_interface.sch]
2020-01-29 generated schematics pdf
2020-01-30 added missing footprints.
    [io_interface.sch, microcontroller_interface.sch, motor_driver.sch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]
2020-02-05 combined 2.54p connectors. changed diode footprint.
    [io_interface.sch, motor_driver.sch]
2020-02-05 finished placement of major components.
    [bldc_motor_cntroller.kicad_pcb]
2020-02-05 adding footprint lib table file.
2020-02-06 fixed a typo
    [motor_driver.sch]
2020-02-06 swapped connections for better routing. highlighted serial gpios.
    [io_interface.sch]
2020-02-06 changed the motor conn. for thicker wires.
    [motor_driver.sch]
2020-02-06 finished placement. reduced pcb size.
    [bldc_motor_cntroller.kicad_pcb]
2020-02-08 increase layer count to 4. routinng cont. swapped motor outputs.
    [bldc_motor_cntroller.kicad_pcb, motor_driver.sch]
2020-02-10 pcb routing cont. swapped 2 motor output pins for better routing.
    [bldc_motor_cntroller.kicad_pcb, power_management.sch]
2020-02-15 added heatsink model in the design
    [bldc_motor_cntroller.sch]
2020-02-15 changed the SMD connector to JST SH (from JST SHL)
    [io_interface.sch]
2020-02-15 finished routing. DRC check pass with some known voilations.
    [bldc_motor_cntroller.kicad_pcb]
2020-02-15 generated pdf for pcb layers and rendered images
2020-02-16 improved assembly documentation
    [bldc_motor_cntroller.kicad_pcb, io_interface.sch, motor_driver.sch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]
2020-02-16 generated gerber and drill files
    [bldc_motor_cntroller-B_Cu.gbr, bldc_motor_cntroller-B_Fab.gbr, bldc_motor_cntroller-B_Mask.gbr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]
2020-02-16 adding the BOM and fab zip file.
    [bldc_motor_cntroller.csv]
2020-02-17 created a sub project for AS5047 encoder pcb. finish sch and pcb
    [bldc_motor_encoder.kicad_pcb, bldc_motor_encoder.sch]
2020-02-17 generated output files for the encode pcb
    [bldc_motor_encoder-B_Cu.gbr, bldc_motor_encoder-B_Mask.gbr, bldc_motor_encoder-B_Paste.gbr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]
2020-03-01 improved BOM
    [bldc_motor_cntroller.csv, bldc_motor_cntroller.sch, io_interface.sch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]
2020-06-23 adding component BOM ( 2x controller pcb, 2x encoder pcb)
    [mouser_bom.xls]
